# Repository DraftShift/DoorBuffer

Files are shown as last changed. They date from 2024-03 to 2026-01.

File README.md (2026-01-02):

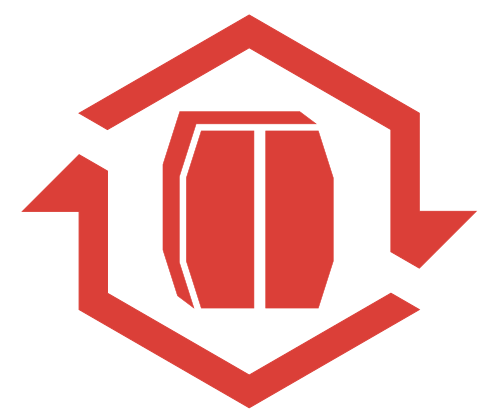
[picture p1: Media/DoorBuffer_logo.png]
#  DoorBuffer V2


&nbsp;&nbsp;&nbsp;&nbsp;&nbsp;&nbsp;


## 🌐 Official Website

StealthChanger now has an official website!

👉 **https://stealthchanger.com** 

##
Simple printable doorbuffer to claw back 15-20mm without upgrading the front frame. 

## WARNING: Calibrate shrinkage before you print. These are long pieces and errors will show.

### Now supports stock, Clacky, and Micron rev 1 doors

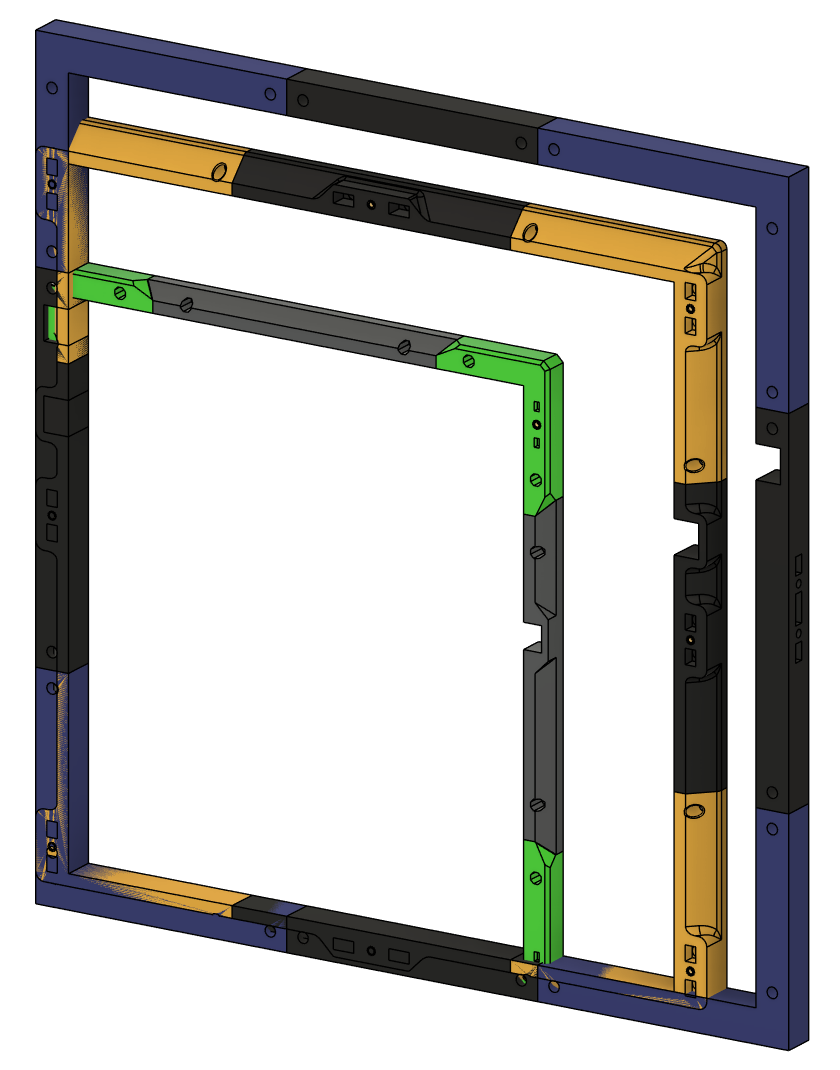
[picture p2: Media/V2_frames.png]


## BOM
Aditional hardware outside the doors
### Stock voron doors
* 22x M3 T-Nut
* 20x M3x8mm SHCS to hold the bracket
* 2x M3x20mm to hold the crossbar
* 8x M3 heat inserts for door mounting
### Klicky-Clack
* 22x M3 T-Nut
* 20x M3x8mm SHCS to hold the bracket
* 2x M3x20mm to hold the crossbar
* 6x M3 heat inserts for door 
### Micron
* 18x M3 nut
* 16x M3x8mm SHCS to hold the bracket
* 2x M3x16mm to hold the crossbar
* 4x M3 heat inserts for door 
* 2x M3x6mm FHCS for door magnets

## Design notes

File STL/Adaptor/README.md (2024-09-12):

# Doorbuffer Adapters

This mod allows you to use extrusions that are cut to the inside length of your front frame.

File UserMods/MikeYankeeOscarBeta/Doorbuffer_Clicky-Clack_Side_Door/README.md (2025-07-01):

# Doorbuffer Clicky-Clack Side Door

The Stock Voron V2 doors suck. Adding an additional 20mm more out the front to mount Clicky-Clack fridge door not too tempting?
Want to have access to your umbilicals and electronics on the back?
Feel like the docks are in the way when reaching for prints?

Add a ClickyClacky Fridge Door to the side of your printer instead with this mod!

## Description:
This Usermod replaces the right top and bottom corners of the door-buffer and uses most of the original parts from the Clicky-Clack Fridge door mod: https://github.com/tanaes/whopping_Voron_mods/blob/main/clickyclacky_door%2FREADME.md
Recommend using these hinges to move the side panel to the front so it's easily removeable: https://github.com/DraftShift/DoorBuffer/tree/main/UserMods/MikeYankeeOscarBeta/Doorbuffer_Side_Door_latches

It's designed for a 300 size Voron V2 with the normal height door-buffer, but should fit the other printer sizes for normal height docks.

by 
[MikeYankeeOscarBeta](https://github.com/MikeYankeeOscarBeta/) (VoronDesign Discord: #MikeyMike V2.5796, Voron Toolchangers Discord: MikeyMike - Github: [MikeYankeeOscarBeta](https://github.com/MikeYankeeOscarBeta/StealthChanger))
DraftShiftDesign Discord - user-project thread:    https://discord.com/channels/1226846451028725821/1243948065208008705

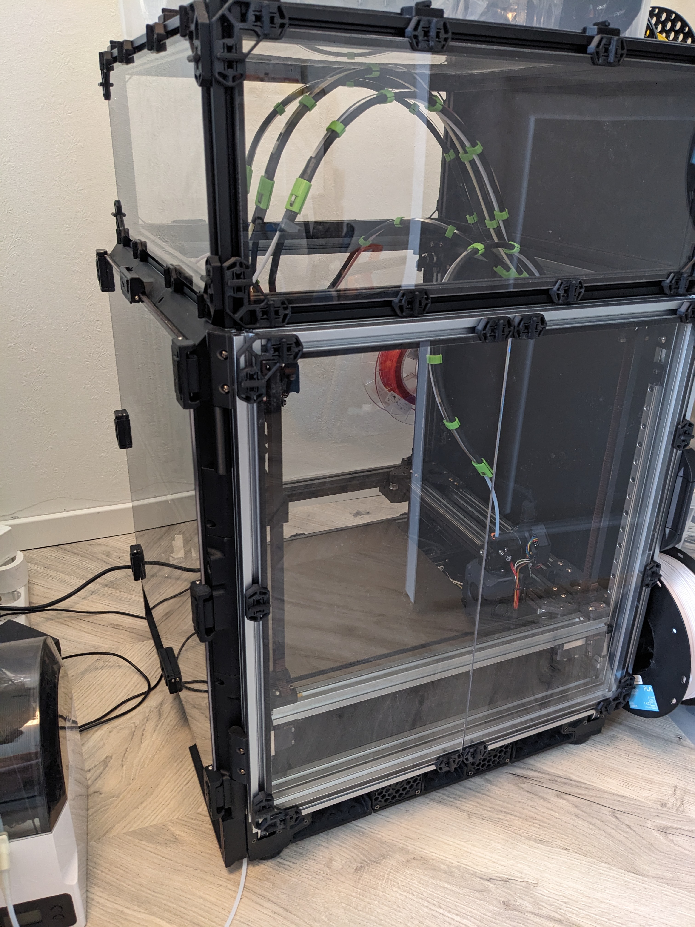
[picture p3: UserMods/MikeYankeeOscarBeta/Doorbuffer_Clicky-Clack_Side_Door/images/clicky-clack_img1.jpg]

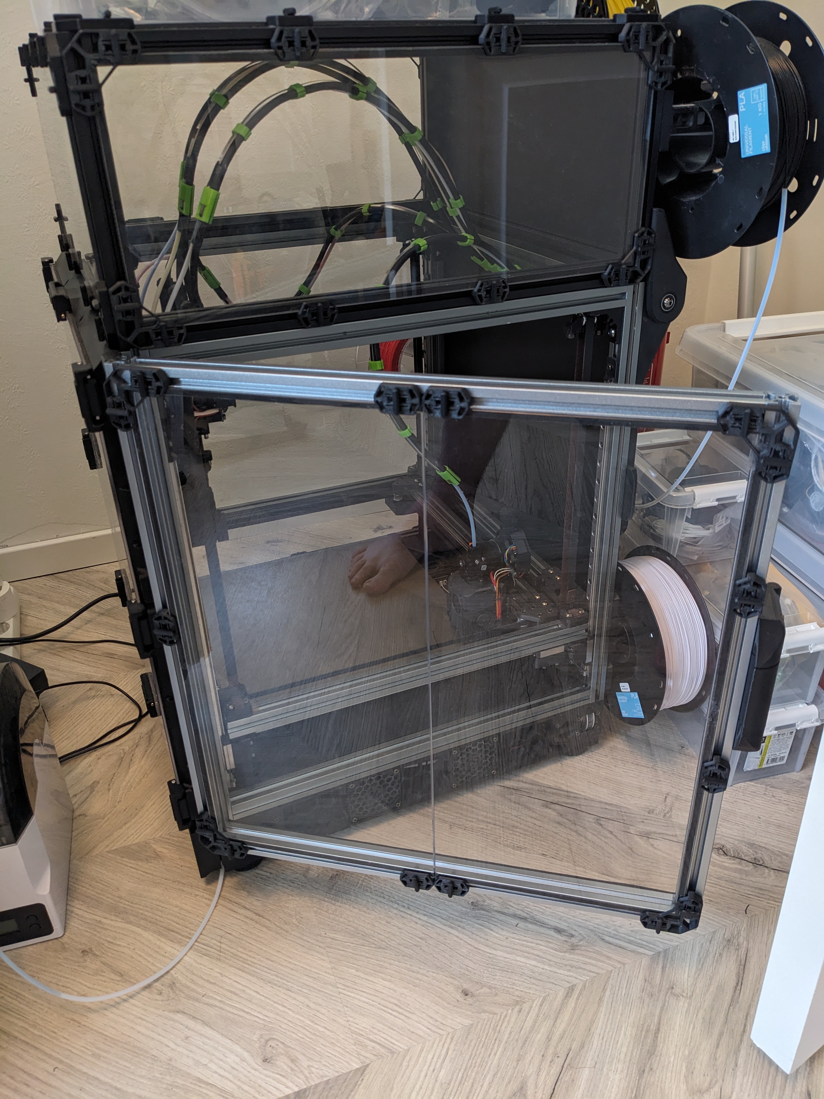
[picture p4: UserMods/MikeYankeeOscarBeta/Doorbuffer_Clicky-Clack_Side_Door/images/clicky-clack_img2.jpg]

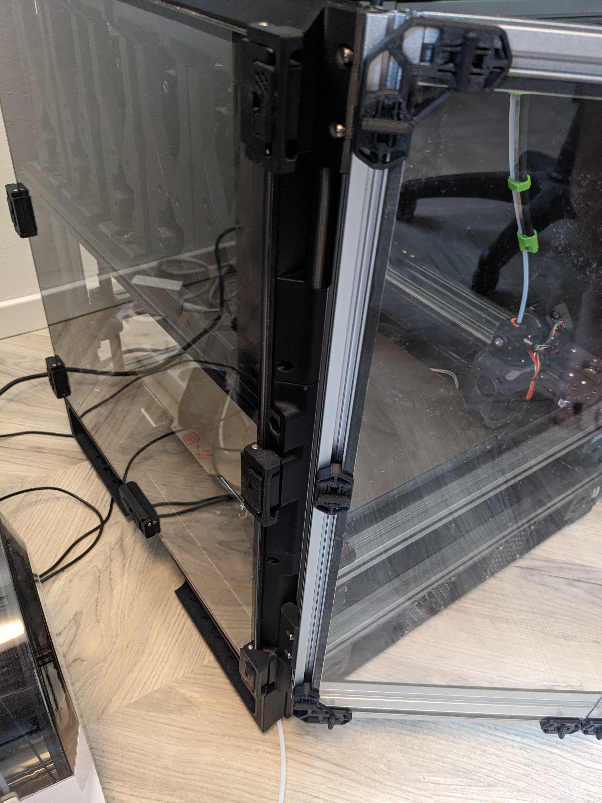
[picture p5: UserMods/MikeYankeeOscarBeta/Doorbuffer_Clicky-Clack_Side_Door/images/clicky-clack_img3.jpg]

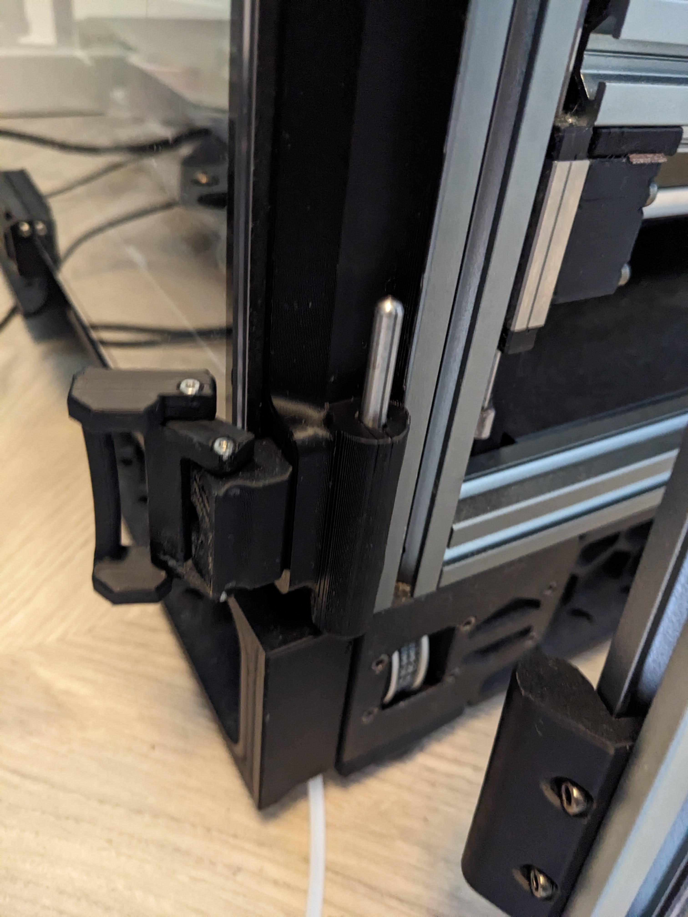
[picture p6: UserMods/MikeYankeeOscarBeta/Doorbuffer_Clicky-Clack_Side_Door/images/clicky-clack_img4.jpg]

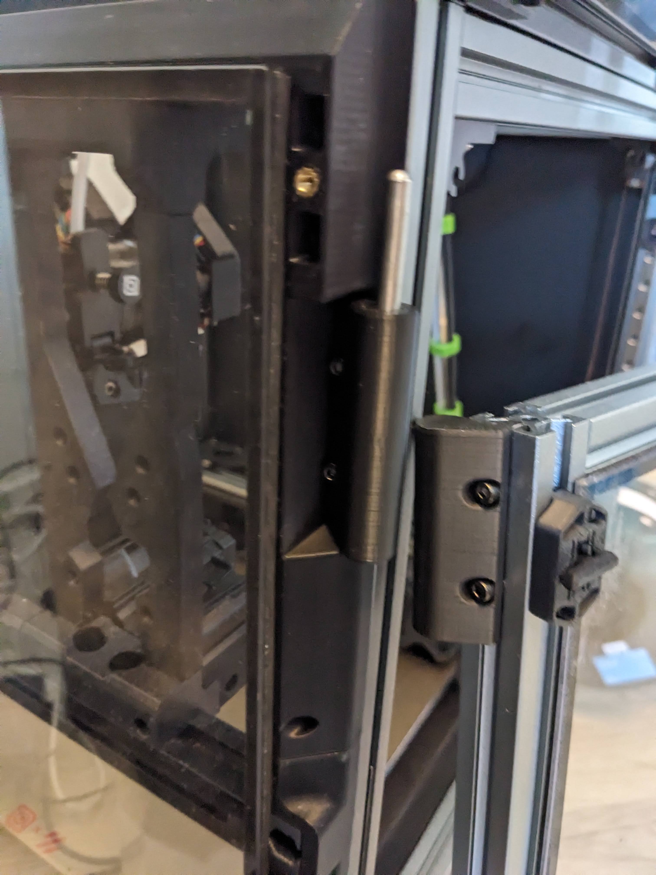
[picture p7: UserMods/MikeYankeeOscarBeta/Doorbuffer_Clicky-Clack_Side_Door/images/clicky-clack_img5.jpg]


## Parts to print:
- 1x doorbuffer-300-clickyclacky-sidedoor_A_v2.stl
- 1x doorbuffer-300-clickyclacky-sidedoor_A_v2.stl

## BOM:
Unchanged. It uses all the same hardware as door buffer and clicky-clack fridge door.

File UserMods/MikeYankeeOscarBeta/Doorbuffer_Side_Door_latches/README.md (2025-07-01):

# Doorbuffer Side Door Latches

Swap your door with your sidepanel with two door-buffers and some clips.

A simple blank and a remix of RichardM's amazing snap latches 
[Voron 2.4 Filament Latch (or any 2020 extrusion)](https://www.printables.com/model/172368-voron-24-filament-latch-or-any-2020-extrusion)  
- remixed for m2 screws and 5.5mm (3mmpanel + 3mm foam - 0.5mm compression)

by 
[MikeYankeeOscarBeta](https://github.com/MikeYankeeOscarBeta/) (VoronDesign Discord: #MikeyMike V2.5796, Voron Toolchangers Discord: MikeyMike - Github: [MikeYankeeOscarBeta](https://github.com/MikeYankeeOscarBeta/StealthChanger))
DraftShiftDesign Discord - user-project thread:    https://discord.com/channels/1226846451028725821/1243948065208008705

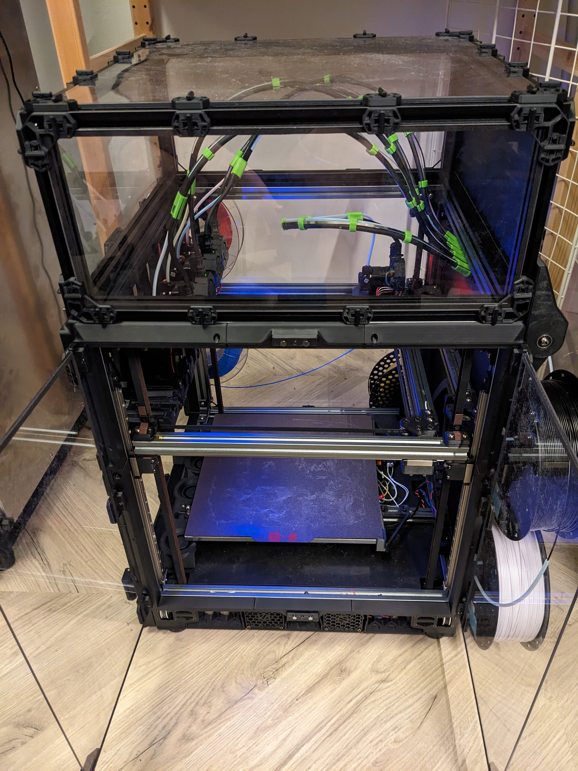
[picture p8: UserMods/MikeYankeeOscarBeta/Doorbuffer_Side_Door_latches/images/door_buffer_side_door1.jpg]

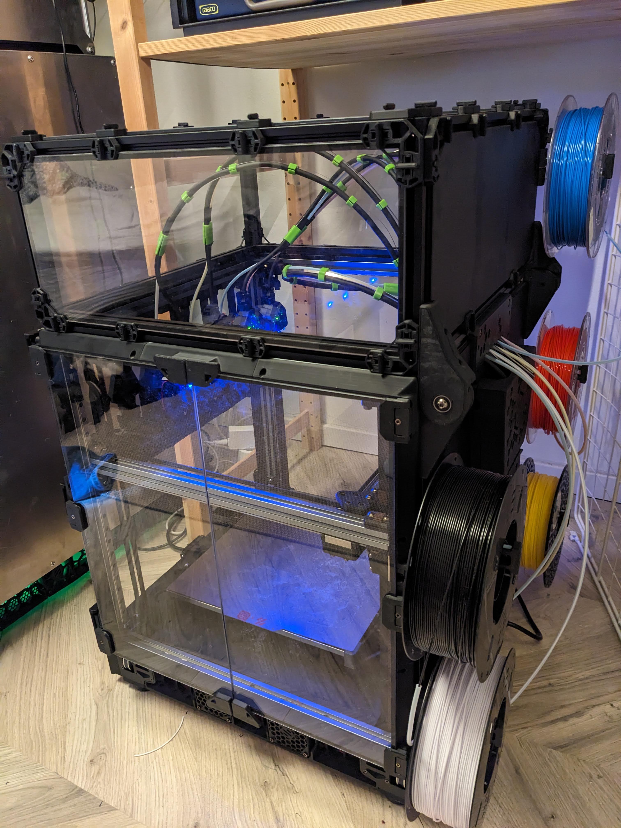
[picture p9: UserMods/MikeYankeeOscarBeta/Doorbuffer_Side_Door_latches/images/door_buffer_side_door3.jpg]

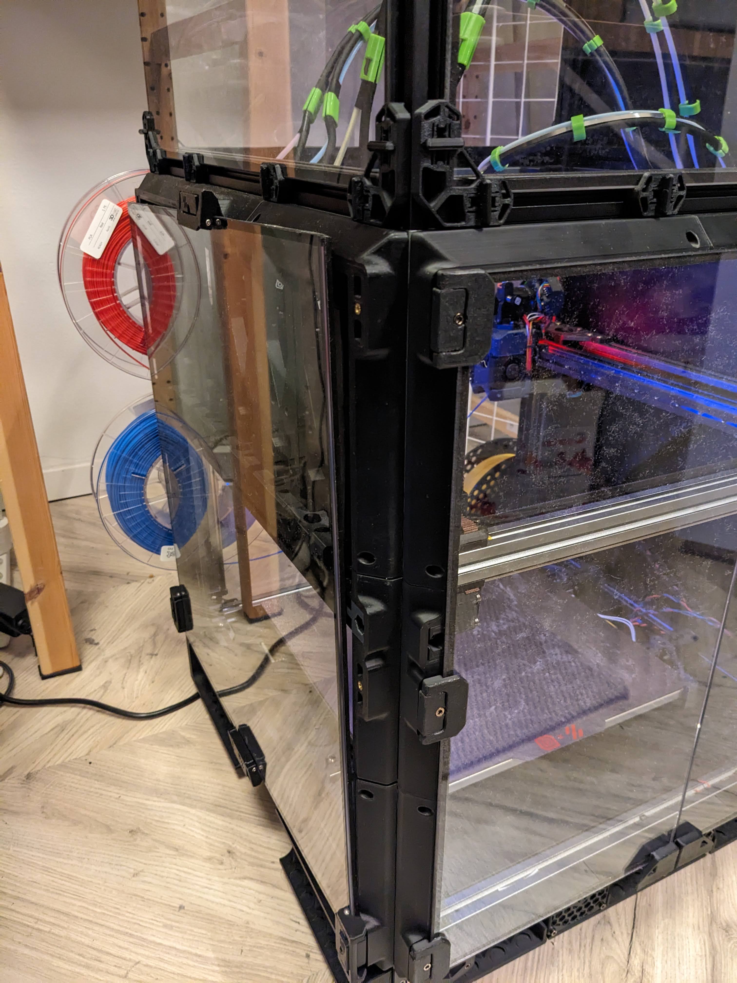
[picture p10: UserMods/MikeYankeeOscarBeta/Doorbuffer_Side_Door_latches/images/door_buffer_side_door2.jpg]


## Parts to print:
- 2x Door Buffer
- 2x NewLatchWithHandle_m2x10mmSHCS_screw_normal_size_3mm_panel_3mm_foam_2_long.stl
- 6x NewLatchWithHandle_m2x10mmSHCS_screw_normal_size_3mm_panel_3mm_foam_2.stl
- 2x 2020_doorbuffer_adapter_blank_for_M5x16_BHCS_x2.stl

## BOM per latch (need 6 latches in total):
| Part | for | Amount | Description|
|---|---|---|-|
| M3x12-14mm BHCS/SHCS Screw  | latch | 6 | M3 BHCS/SHCS screw |
| M2x15mm SHCS Screw | latch | 4 | M2 SHCS screw |
| M3x25mm SHCS Screw | latch | 4 | M2 SHCS screw |
| M5x16 BHCS Screw | Adapter | 2 | M5 BHCS/SHCS |

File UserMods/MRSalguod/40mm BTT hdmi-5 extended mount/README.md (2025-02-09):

An extended bbt hdmi-5 mount for use with the [Clicky-Clack Fridge Door](https://github.com/tanaes/whopping_Voron_mods/tree/main/clickyclacky_door) 
and the [DraftShift Design](https://github.com/DraftShift) [Door Buffer v2](https://github.com/DraftShift/DoorBuffer).   [(Printables Link)](https://www.printables.com/model/1066444)

Print with regular voron recommended settings.

You will need to print 1 of each of the parts from the STL folder. No supports needed.   

Remixed from @DETMan's BTT HDMI5 Mount for Clicky Clack Door for use with the DraftShift Design Door Buffer.   [(Printables Link)](https://www.printables.com/model/861544)

Whom remixed it from @EDnation.   [(Printables Link)](https://www.printables.com/model/787236)

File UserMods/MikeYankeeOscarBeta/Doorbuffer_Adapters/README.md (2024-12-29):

# Doorbuffer Adapters for Monolith_Crossbar
based on DoorBuffer Adapter by [TheSin-](https://github.com/TheSin-/) 

Monolith AWD mod by [MikeYankeeOscarBeta](https://github.com/MikeYankeeOscarBeta/) (VoronDesign Discord: #MikeyMike V2.5796, Voron Toolchangers Discord: MikeyMike - Github: [MikeYankeeOscarBeta](https://github.com/MikeYankeeOscarBeta/StealthChanger))
DraftShiftDesign Discord - user-project thread:    https://discord.com/channels/1226846451028725821/1243948065208008705

This mod allows you to use extrusions that are cut to the inside length of your front frame for monolith adapters.

### Only tested with R0 Printed Monolith AWD (pre-live shaft version)

Printable adapters for crossbar to clear monolith AWD front motors for Voron V2 with StealthChanger

Have to cut the 2020 to size.
The monolith AWD motors take 45mm on each side so the 2020 has to be 90mm shorter than the frames horizontal extrusions

## BOM:
| Part | Amount | Description |
|---|---|---|
| M3 T-slot nut | 4 | Any M3 2020 T-Slot Nut will work (recommend springnuts) |
| M5x15mm BHCS/SHCS Screw | 2 | M5 BHCS/SHCS socket head screw, 15mm minimum (longer is better if you can tap the extrusion deeper than 10mm) |
| M3x20mm SHCS Screw | 4 | M3 screw, BHCS will also work |
| 2020 extrusion | 1 | 2020 extrusion cut to length (see table below), tapped on both ends. Misumi#: HFS5-2020-380-TPW  / HFSB5-2020-380-TPW |
| M3x25mm SHCS Screw | 4 | M3 screw, BHCS will also work |

### Extrusion lengths for Stock V2 sizes:
| Model | Calculation | Monolith AWD Crossbar extrusion length |
|---|---|---|
| Voron V2-350 | 470.00 mm - 90mm | 380 mm |
| Voron V2-300 | 420 mm - 90mm | 330 mm |
| Voron V2-250 | 370 mm - 90mm | 280 mm |
| Voron V2-custom size  | [horizontal extrusion length] - 90mm | x mm |

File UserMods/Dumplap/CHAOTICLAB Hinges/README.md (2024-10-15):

Door Buffer modified to fit the 2 hinge CNC door hinges from CHAOTICLAB

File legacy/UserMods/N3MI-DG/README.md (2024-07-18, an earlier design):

# Short Frame Buffer Mod

This mod add door buffer support for <a href="https://github.com/DraftShift/ModularDock/tree/main/UserMods/BlackShade/ShortFrame">BlackShade's Short Frame Dock Mod</a> for both 300mm and 350mm frames. It replaces the left and right middle sections of the door buffer and both T slot (default) and V slot versions are provided.

### Extra BOM
2x M3 6mm SHCS screws

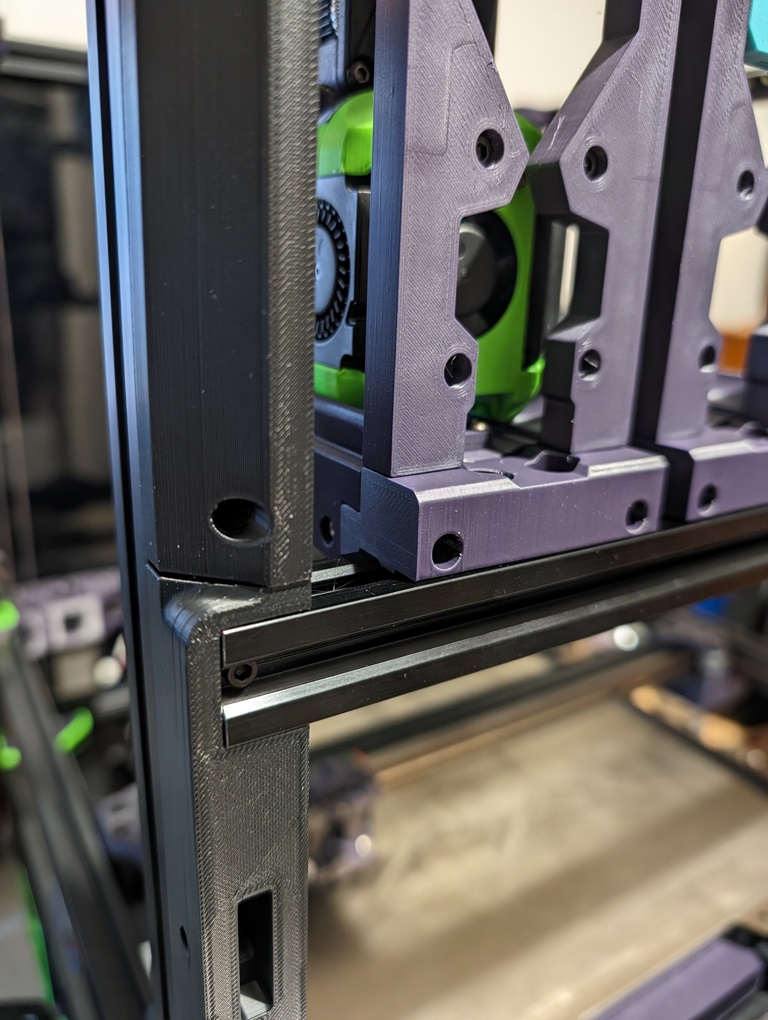
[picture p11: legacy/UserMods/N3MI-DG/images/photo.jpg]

<br/>
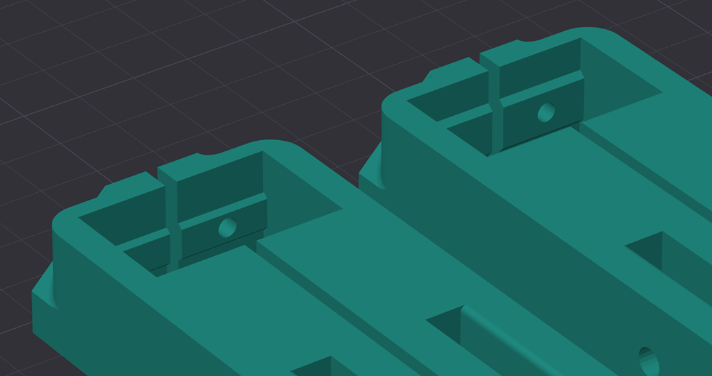
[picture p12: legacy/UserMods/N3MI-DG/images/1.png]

<br/>
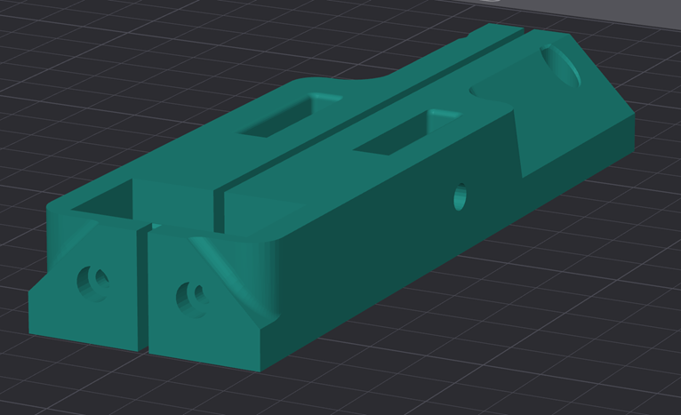
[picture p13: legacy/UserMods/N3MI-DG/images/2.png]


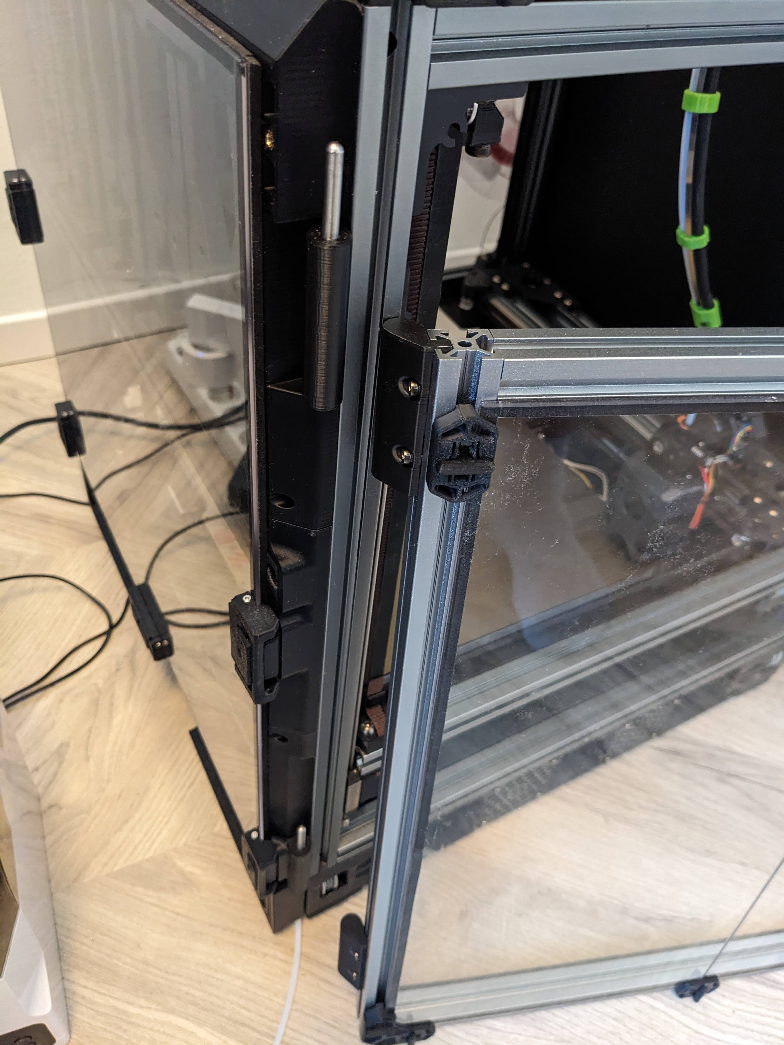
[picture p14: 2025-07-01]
UserMods/MikeYankeeOscarBeta/Doorbuffer_Clicky-Clack_Side_Door/images/clicky-clack_img6.jpg

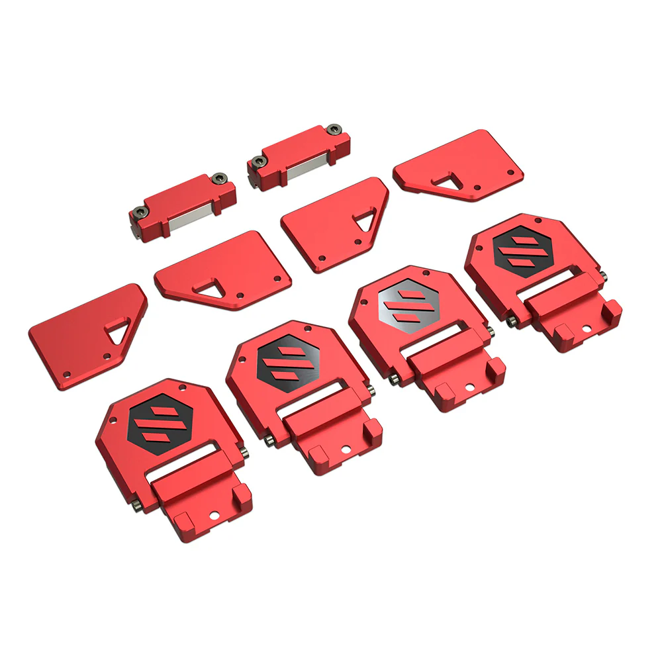
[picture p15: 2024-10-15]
UserMods/Dumplap/CHAOTICLAB Hinges/Media/CNChing.png

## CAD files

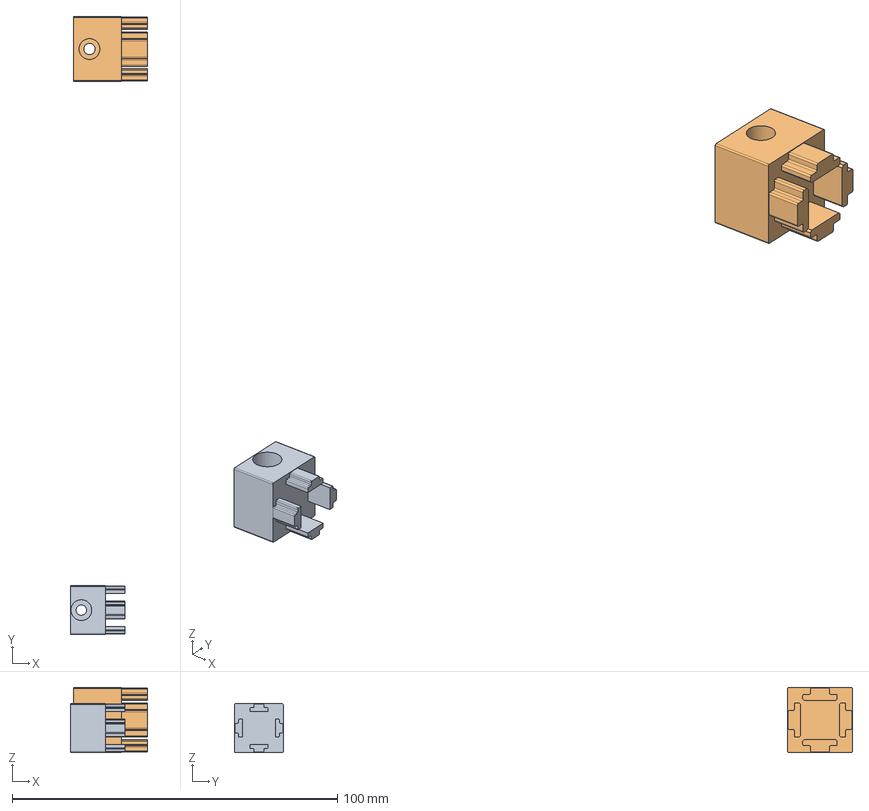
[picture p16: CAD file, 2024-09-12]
CAD/Doorbuffer_Adapters.step
23.8 x 190.0 x 20.0 mm
1515_doorbuffer_adapter_x2
2020_doorbuffer_adapter_x2

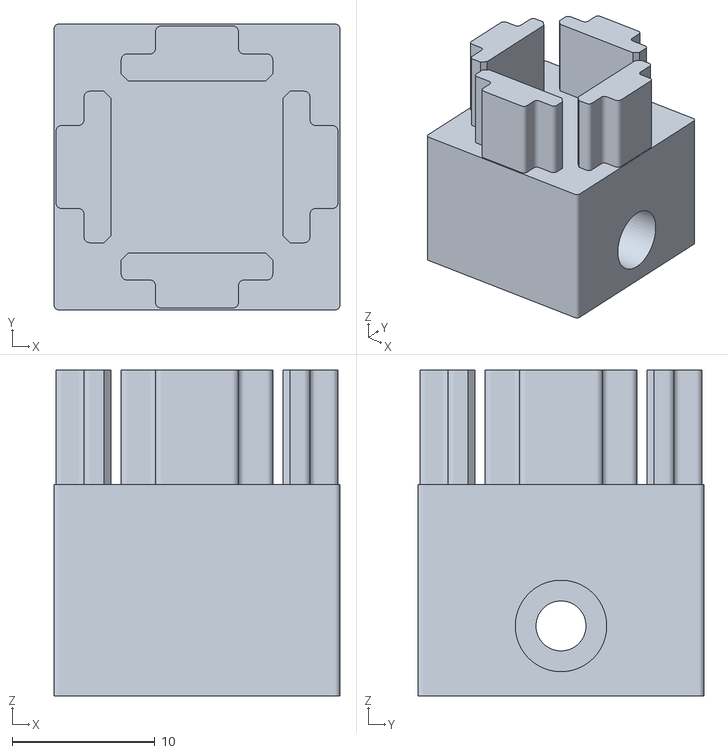
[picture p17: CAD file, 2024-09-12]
STL/Adaptor/2020_doorbuffer_adapter_x2.stl
20.0 x 20.0 x 22.8

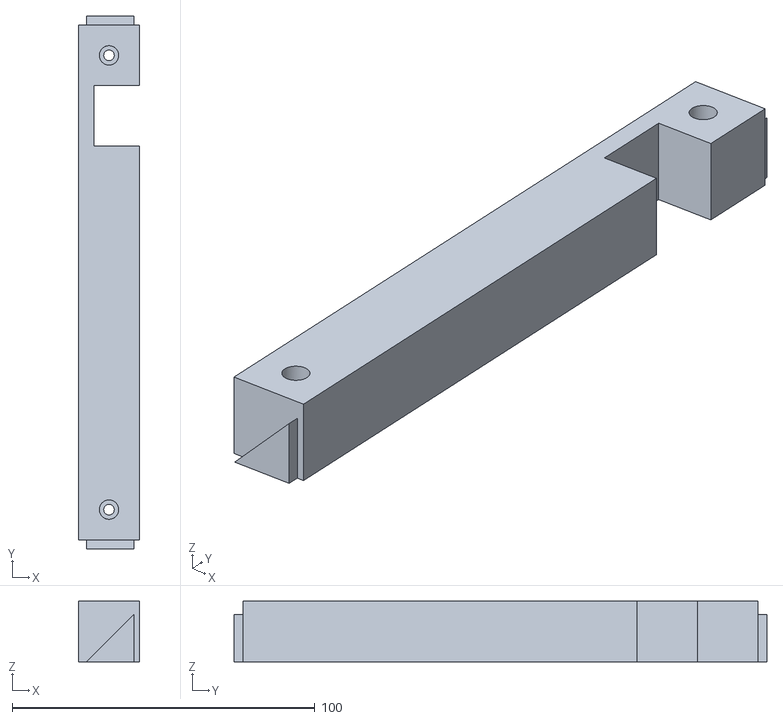
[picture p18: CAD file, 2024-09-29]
STL/Clicky-Klack/Short docks/250/Left.stl
20.0 x 176.0 x 20.0

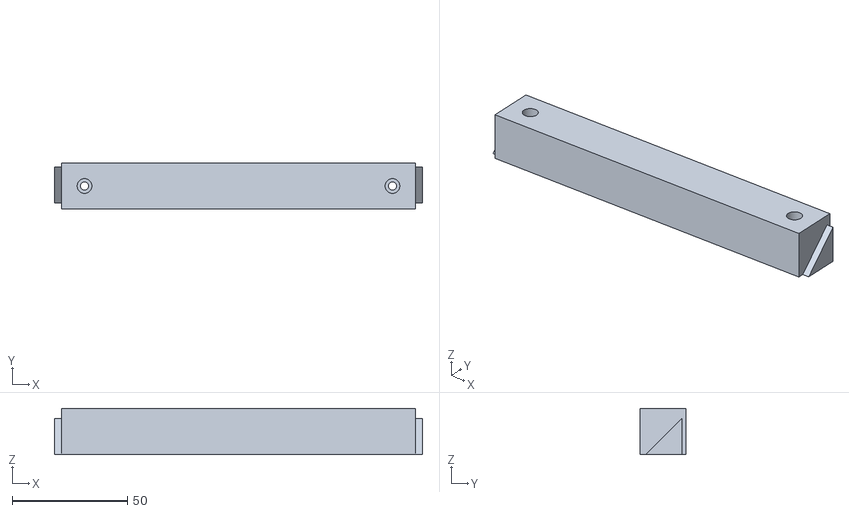
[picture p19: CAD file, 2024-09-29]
STL/Clicky-Klack/Short docks/300/Bottom.stl
159.3 x 20.0 x 20.0

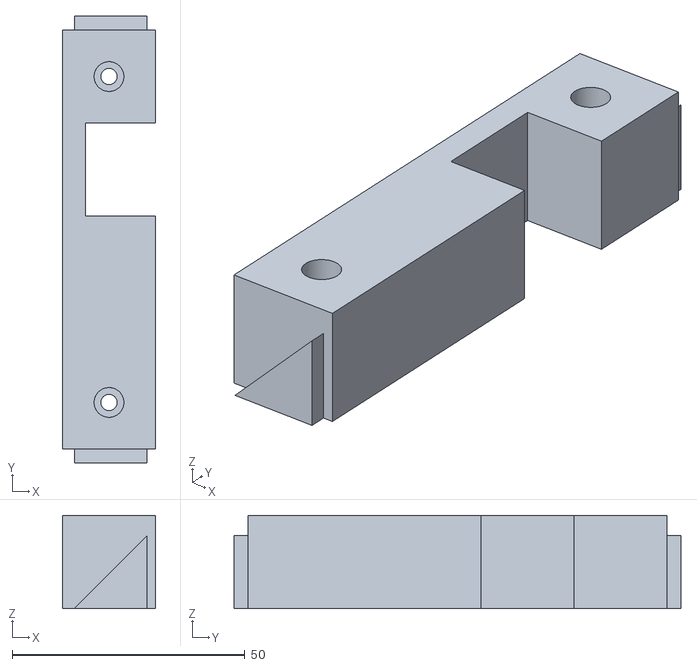
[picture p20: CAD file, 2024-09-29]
STL/Clicky-Klack/Standard docks/250/Left.stl
20.0 x 96.0 x 20.0

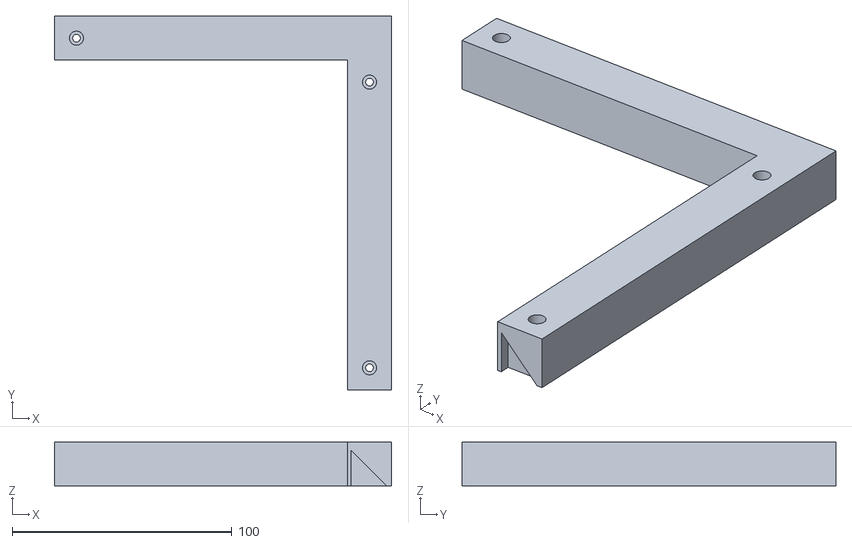
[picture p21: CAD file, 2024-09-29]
STL/Clicky-Klack/Standard docks/300/Top right corner.stl
153.3 x 170.0 x 20.0

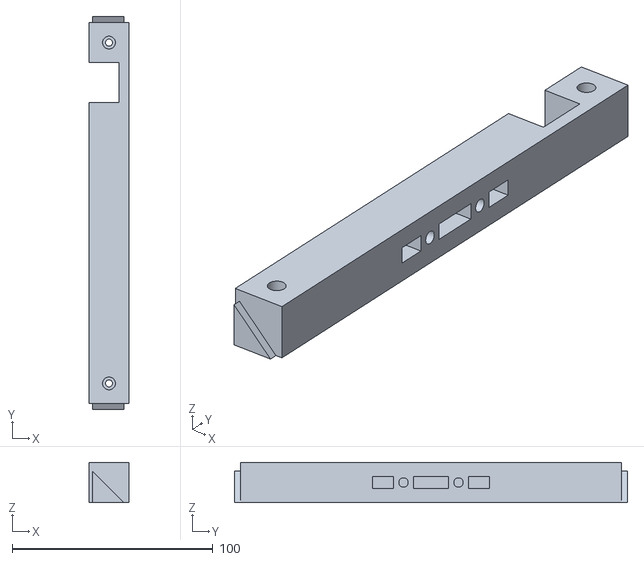
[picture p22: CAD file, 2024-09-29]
STL/Clicky-Klack/Standard docks/350/Right.stl
20.0 x 196.0 x 20.0

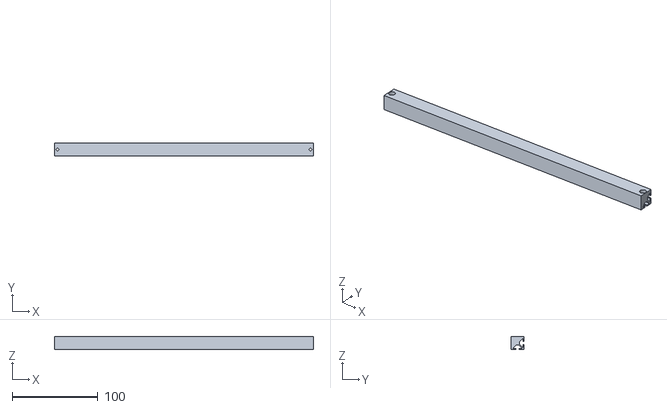
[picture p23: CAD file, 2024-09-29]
STL/Micron/Micron dockbar.stl
302.0 x 15.0 x 15.0

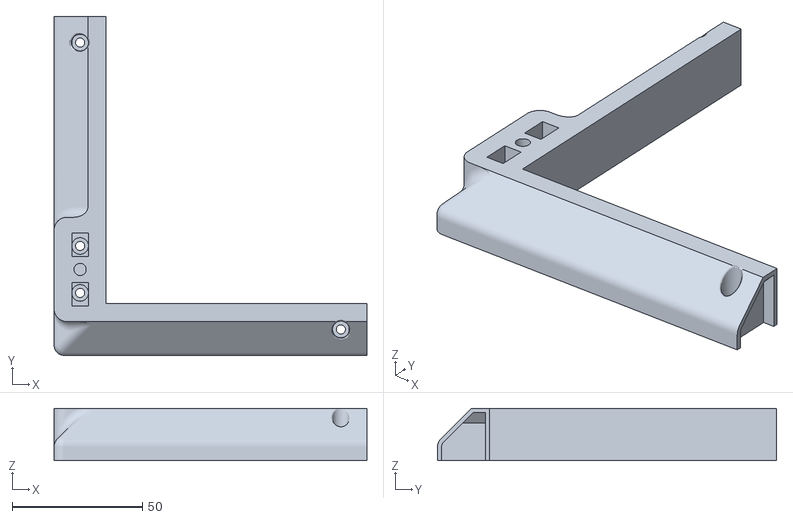
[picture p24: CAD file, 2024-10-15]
STL/Stock Voron/Short docks/300/Bottom left corner.stl
120.0 x 130.0 x 20.0

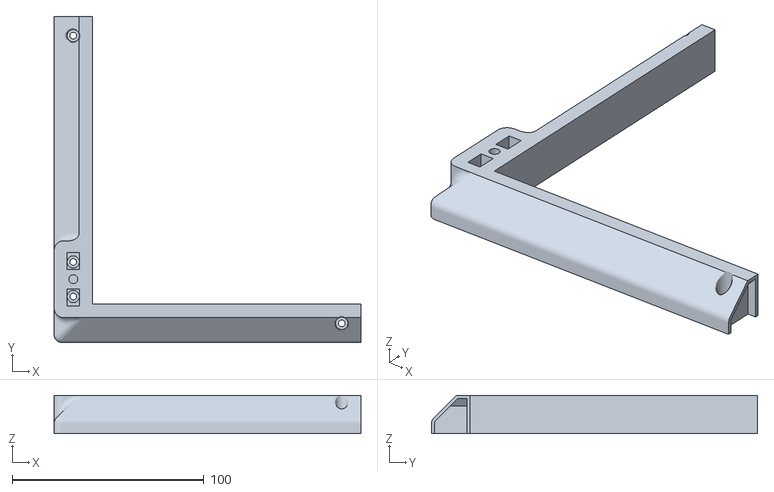
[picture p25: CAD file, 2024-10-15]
STL/Stock Voron/Standard docks/300/Bottom left corner.stl
160.0 x 170.0 x 20.0

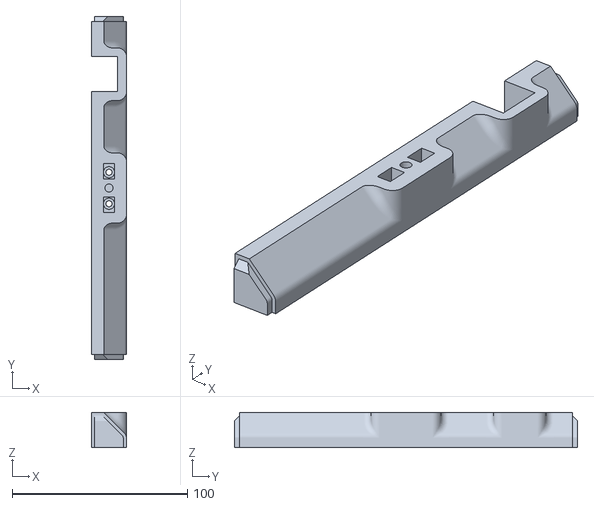
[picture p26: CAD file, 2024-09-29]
STL/Stock Voron/Standard docks/350/Left.stl
20.0 x 196.0 x 20.0

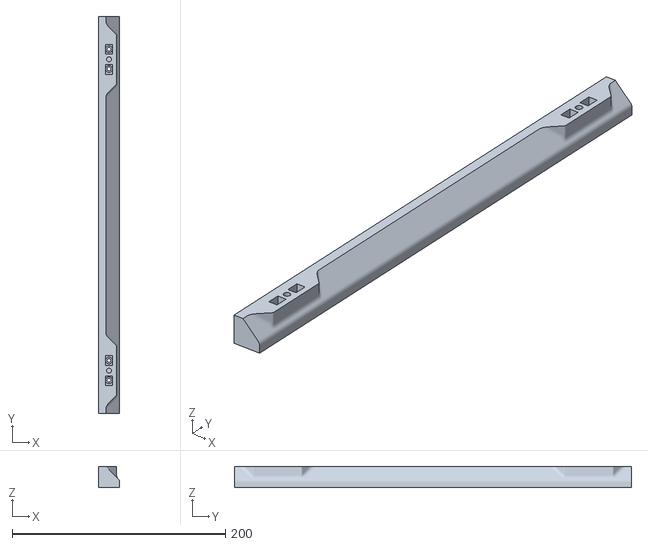
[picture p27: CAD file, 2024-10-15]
UserMods/Dumplap/CHAOTICLAB Hinges/STL/Right.stl
20.0 x 372.2 x 20.0

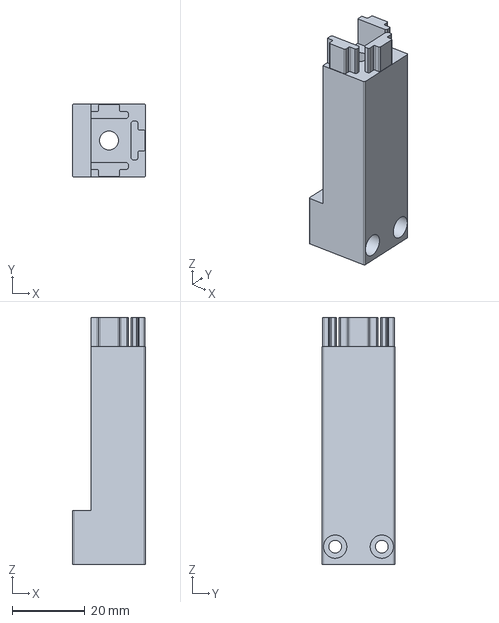
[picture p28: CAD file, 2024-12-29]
UserMods/MikeYankeeOscarBeta/Doorbuffer_Adapters/CAD/2020_doorbuffer_adapter_monolith.step
20.0 x 20.0 x 67.8 mm

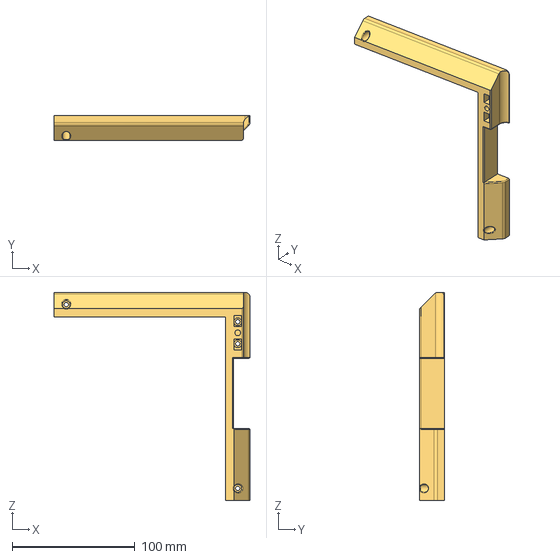
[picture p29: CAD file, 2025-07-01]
UserMods/MikeYankeeOscarBeta/Doorbuffer_Clicky-Clack_Side_Door/CAD/doorbuffer-300-clickyclacky-sidedoor_B_v2.step
160.0 x 20.0 x 170.0 mm

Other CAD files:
STL/Clicky-Klack/Short docks/350/Top.stl
STL/Stock Voron/Short docks/250/Top.stl
STL/Stock Voron/Short docks/350/Bottom right corner.stl
STL/Stock Voron/Standard docks/250/Bottom.stl
STL/Adaptor/1515_doorbuffer_adapter_x2.stl
STL/Clicky-Klack/Short docks/250/Bottom left corner.stl
STL/Clicky-Klack/Short docks/250/Bottom right corner.stl
STL/Clicky-Klack/Short docks/250/Bottom.stl
STL/Clicky-Klack/Short docks/250/Right.stl
STL/Clicky-Klack/Short docks/250/Top left corner.stl
STL/Clicky-Klack/Short docks/250/Top right corner.stl
STL/Clicky-Klack/Short docks/250/Top.stl
STL/Clicky-Klack/Short docks/300/Bottom left corner.stl
STL/Clicky-Klack/Short docks/300/Bottom right corner.stl
STL/Clicky-Klack/Short docks/300/Left.stl
STL/Clicky-Klack/Short docks/300/Right.stl
STL/Clicky-Klack/Short docks/300/Top left corner.stl
STL/Clicky-Klack/Short docks/300/Top right corner.stl
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

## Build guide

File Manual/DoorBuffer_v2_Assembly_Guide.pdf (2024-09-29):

# Door Buffer V2

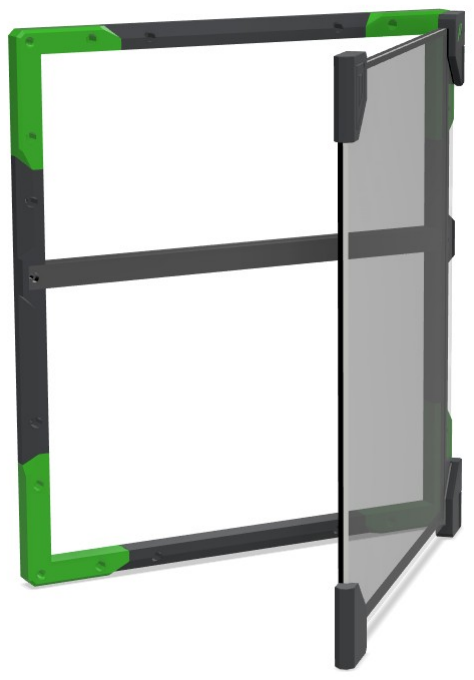
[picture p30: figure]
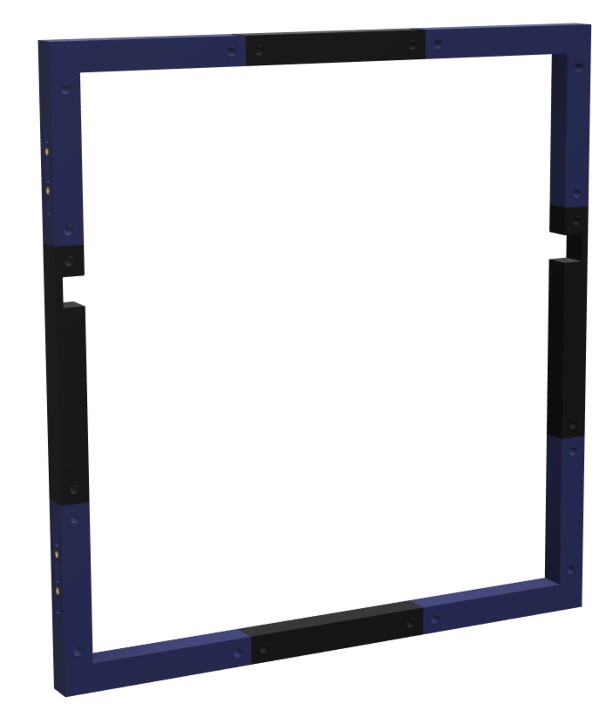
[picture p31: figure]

# Door Buffer V2 BUILD GUIDE

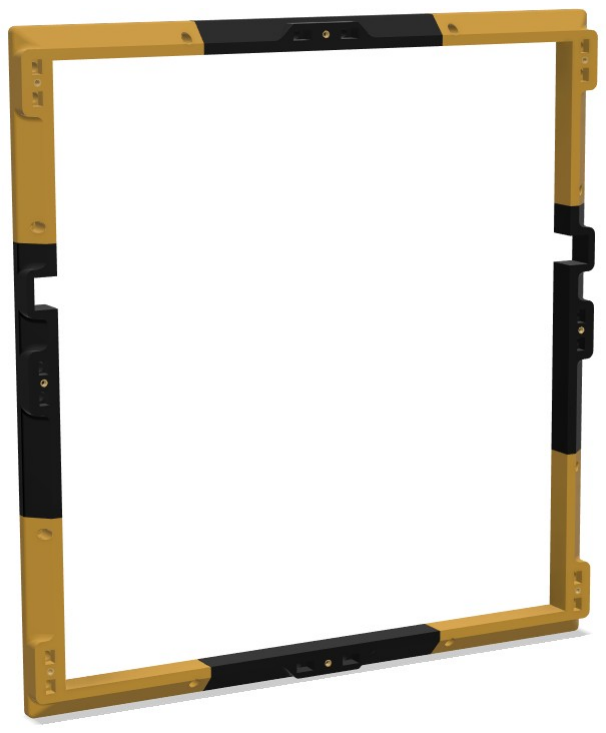
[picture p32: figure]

# Giving you 20mm back, and a more rigid dock (Now with Micron and Clacky support)

# VERSION 2024-09-28

## PREFACE

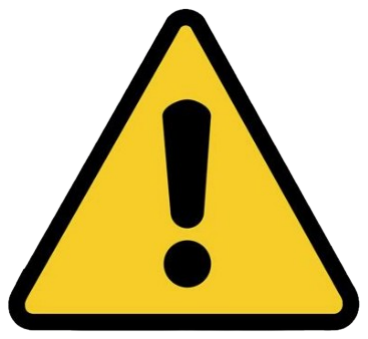
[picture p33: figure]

Before you begin on your journey, a word of caution.

In the comfort of your own home you are about to assemble a robot. This machine can maim, burn, and electrocute you if you are not careful. Please do not become the first STEALTHCHANGER fatality. There is no special Reddit flair for that.

Please, read the entire manual before you start assembly. As you begin wrenching, please check our Discord channels for any tips and questions that may halt your progress.

Most of all, good luck!

THE STEALTHCHANGER TEAM

2

## GITHUB.COM/STEALTHCHANGER/DOORBUFFER

## TABLE OF CONTENTS

Introduction | 04
Hardware | 07
New features | 08
Frame | 9
Heat inserts | 11
Attach to frame | 12
Mounting doors | 13
Parametric editing | 15

3

## INTRODUCTION

PART PRINTING GUIDELINES

The Voron Team has provided the following print guidelines for you to follow in order to have the best chance at success with your parts. The StealthChanger Team recommends to follow the same standards. There are often questions about substituting materials or changing printing standards, but we recommend you follow these:

3D PRINTING PROCESS
Fused Deposition Modeling (FDM)

MATERIAL
ABS

LAYER HEIGHT
Recommended: 0.2mm

EXTRUSION WIDTH
Recommended: Forced 0.4mm

INFILL TYPE
Grid, Gyroid, Honeycomb, Triangle or Cubic

INFILL PERCENTAGE
Recommended: 15% or higher

NOTE: These parts do not experience any load an can be less dense compared to other Voron parts

WALL COUNT
Recommended: 4

SOLID TOP/BOTTOM LAYERS
Recommended: 5

4

## INTRODUCTION

FILE NAMING

By this time you should have already downloaded our STL files from the StealthChanger GitHub. You might have noticed that we have used the Voron naming convention for the files. This is how to use them.

PRIMARY COLOUR

Example part_x4.stl

These files will have nothing at the start of the filename.

ACCENT COLOUR

Example [a]_part.stl

We have added “[a]” to the front of any STL file that is intended to be printed with accent colour.

QUANTITY REQUIRED

Example [a]_part_x4.stl

If any file ends with “_x#”, that is telling you the quantity of that part required to build the machine.

HOW TO GET HELP

If you need assistance with your build, we are here to help. Head on over to our Discord group and post your questions. This is our primary medium to help STEALTHCHANGER Users and we have a great community that can help you out if you get stuck.

### https://discord.gg/Mx9JKbt7

5

## INTRODUCTION

REPORTING ISSUES

Should you find an issue in the documentation or have a suggestion for an improvement please consider opening an issue on GitHub (https://github.com/Stealthchanger/DoorBuffer/issues). When raising an issue please include the relevant page numbers and a short description; annotated screenshots are also very welcome. We periodically update the manual based on the feedback we get.

THIS IS JUST A REFERENCE

This manual is designed to be a simple reference manual and we always recommend downloading the cad-files to look around for yourself.

### https://github.com/Stealthchanger/DoorBuffer

6

## HARDWARE REFERENCE

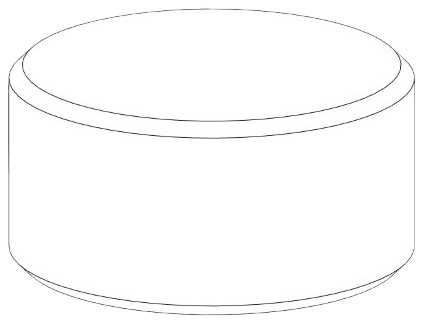
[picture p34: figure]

MAGNET Metric round button neodymium magnet used on the Voron. N52 is highly recommended. | SOCKET HEAD CAP SCREW (SHCS) Metric fastener with a cylindrical head and hex drive. The most common fastener used on the Voron. ISO 4762

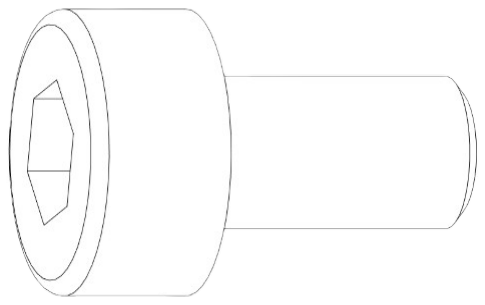
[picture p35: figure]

T-NUT Hammerhead A type of nut that slides into the extrusion rail as a method of affix other parts to it. | HEAT SET INSERT Heat inserts with a soldering tip so that they melt the plastic when installed. As the plastic cools, it solidifies around the knurls and ridges on the insert for excellent resistance to both torque and pull-out.

7

## NEW FEATURES

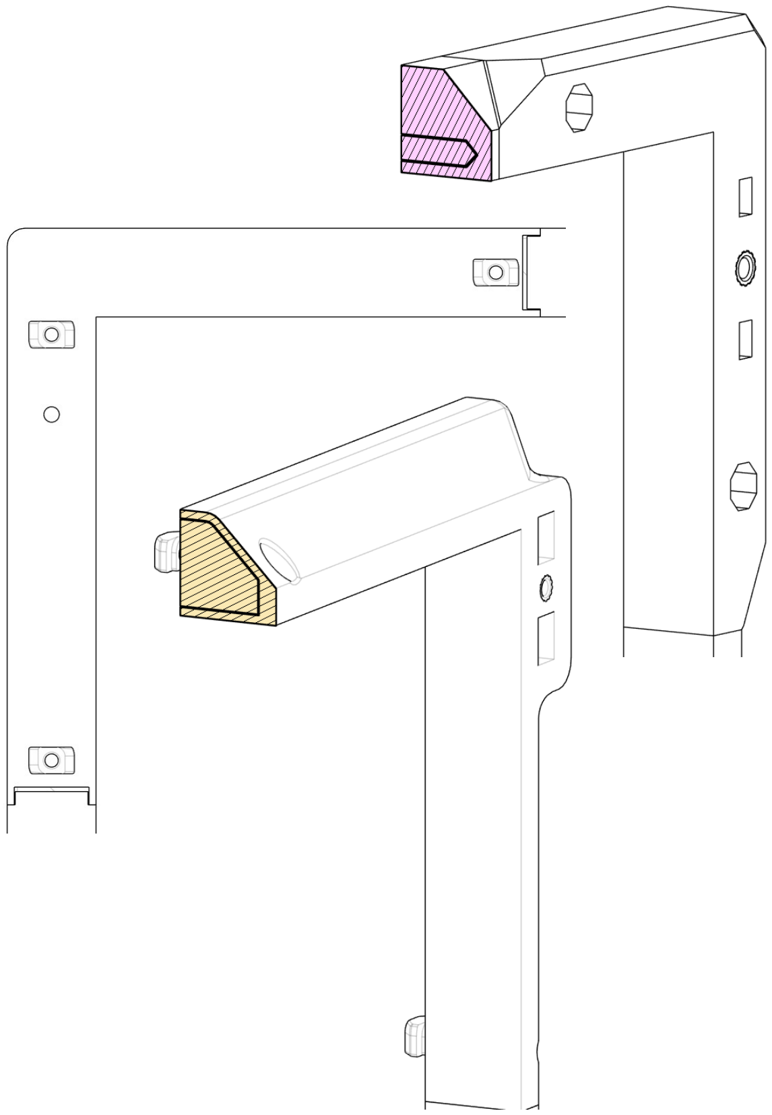
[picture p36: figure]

Stock panels

- Gone are the decorative clips in favour of a simpler design
- Adjustable dockheights (130mm to 170mm) to accommodate stubby docks.

Klacky door

The build now adds klackydoors! This is only a simple plastic 2020 padding, but can be configured with the parametric file if needed.

Micron door!

The micron buffer is designed specifically for short docks.

NOTE: The door is taken from the rev 1 version found on their Github (https://github.com/PrintersForAnts/Micron/tree/main)

Common new features

All variations come with overlapping design to help patch those pesky gaps!

8

## FRAME

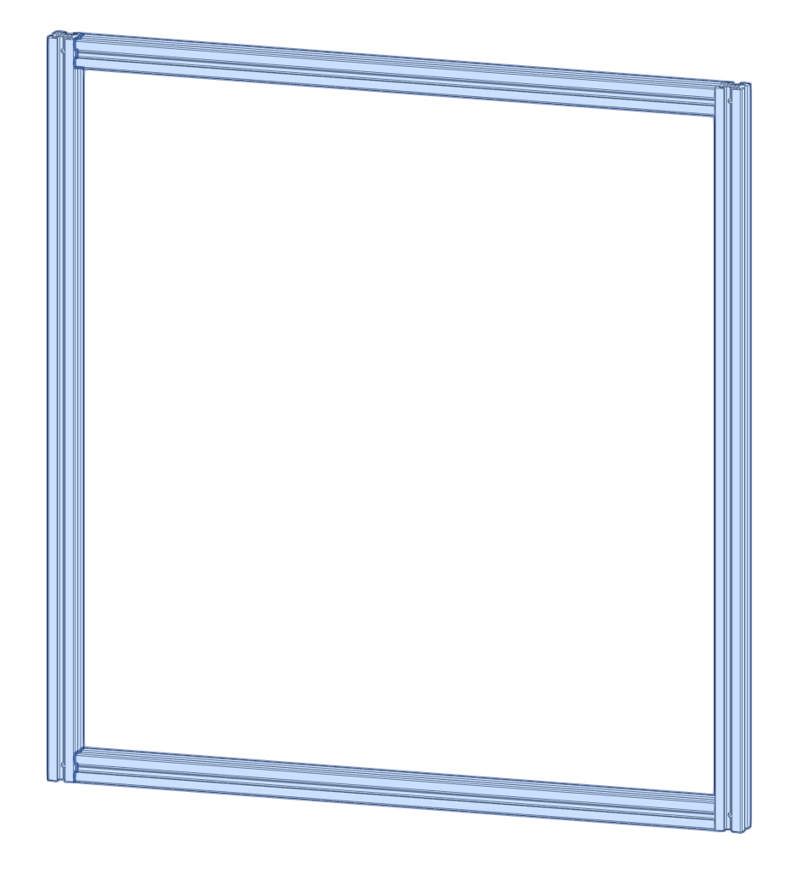
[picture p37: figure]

BASE FRAME

This build is meant to attach onto a normal 2020 V2.4 frame, though if you have a customized one there will be instructions on how to edit this entire design in Fusion360 at the end.

NOTE: before you begin printing, measure to see if your frame is actually up to Voron specs. A few mm off will create gaps in your parts. If its out of spec. Look at the end of this manual and enter your real measurements into the parametric CAD file!

NOTE: Make sure your printer is properly calibrated for dimensions and material shrinkage! As some of these parts can get long a small deviation will give noticeable results!

TOOLBAR HOLE PLACEMENT
The bottom bar that the modular docks mount to is 10mm shorter than your frame measured furthest left to right. A standard 350 frame is 510mm across the front and so the toolbar needs to be 500mm

NOTE: You will need to drill a hole big enough for a 3mm screw to pass through 4mm minimum is recommended for better adjustment.

NOTE:
Micron bar is 302mm. 8Mm shorter than the total width of the micron.

9

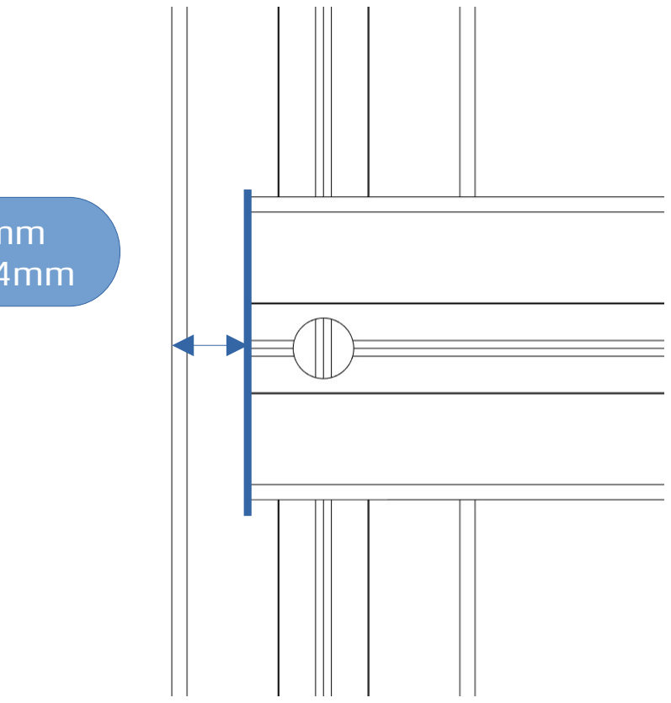
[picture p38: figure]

2.4 = 5mm

## Micron = 4mm

## FRAME

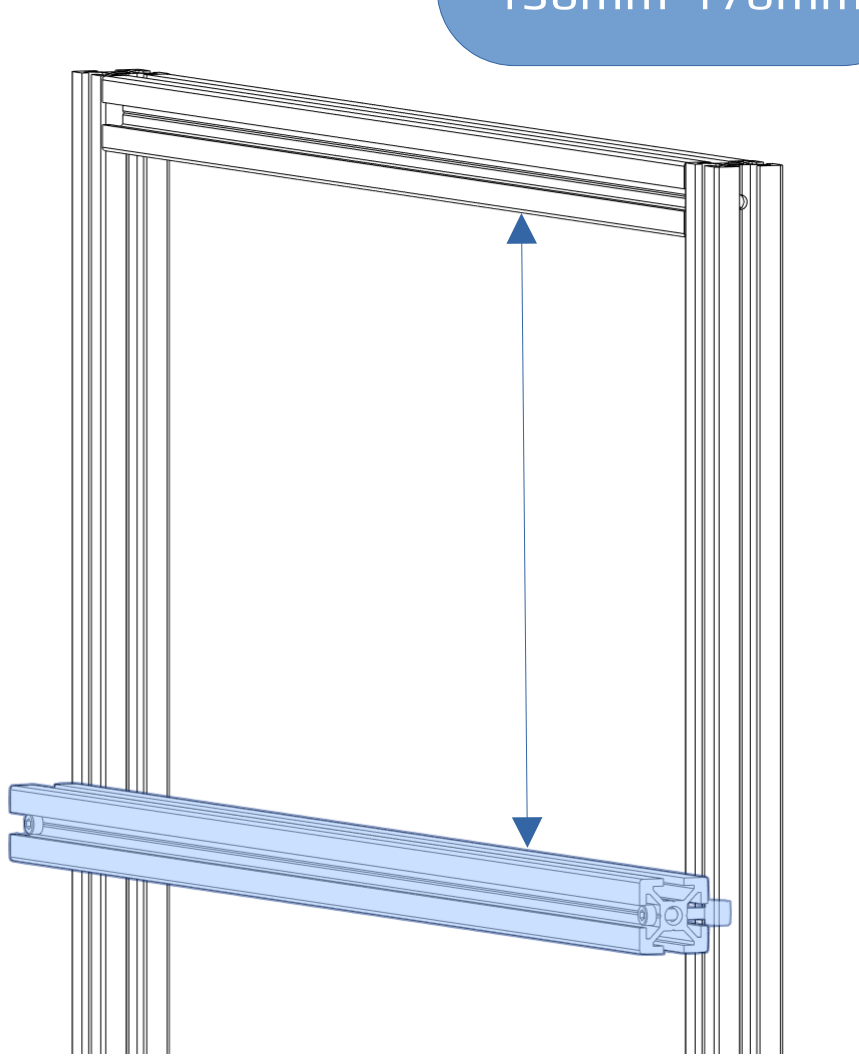
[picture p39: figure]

TOOLBAR TO FRAME

The new V2 buffer supports any dock height from 130mm to 170mm so make sure you bolt on the extrusion at correct height.

NOTE:
- For a standard dock height, use 170mm
- For stubby docks, use 130mm

EXTRA NOTE:
Micron only supports 130mm docks!

## 130mm-170mm

SCREWS

Take your M3x20mm through the holes you made and mount it using T-NUT’s

## M3x20mm SHCS T-NUT

10

ATTENTION MICRON BUILDERS!

For preloading nuts you have to add 4xM3 nuts to BOTH top and bottom horizontal extrusions, the vertical ones have free access and can be added later without worry.

Also for attaching the extrusion M3x12mm or 16mm may be needed depending on your extrusion profile. Check clearances and potentially add a washer for correct spacing

## Heat inserts

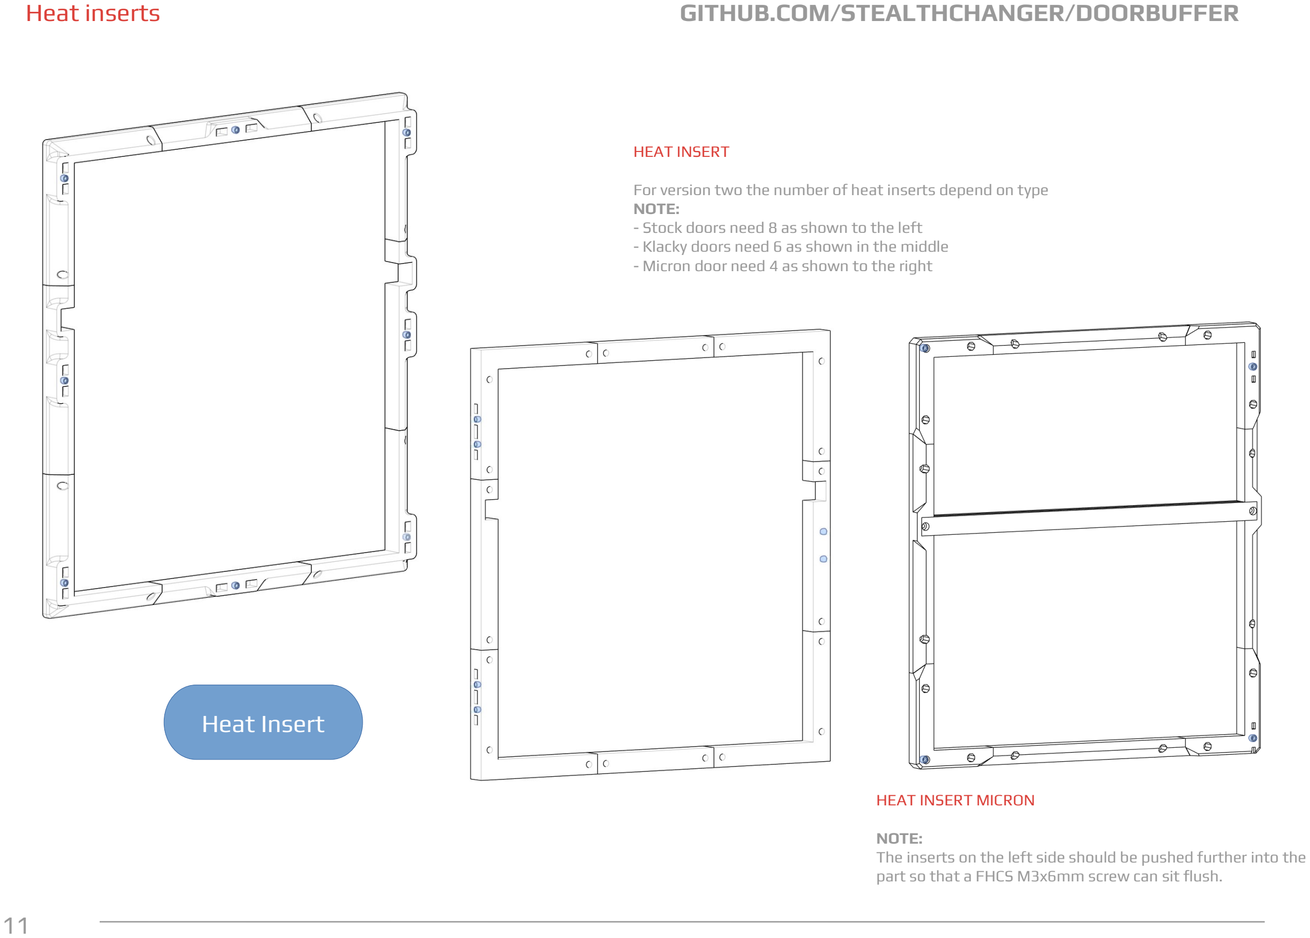
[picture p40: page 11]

HEAT INSERT

For version two the number of heat inserts depend on type NOTE:
- Stock doors need 8 as shown to the left
- Klacky doors need 6 as shown in the middle
- Micron door need 4 as shown to the right

11

## Heat Insert

HEAT INSERT MICRON

NOTE:
The inserts on the left side should be pushed further into the part so that a FHCS M3x6mm screw can sit flush.

## Attach to frame

## M3x8 SHCS

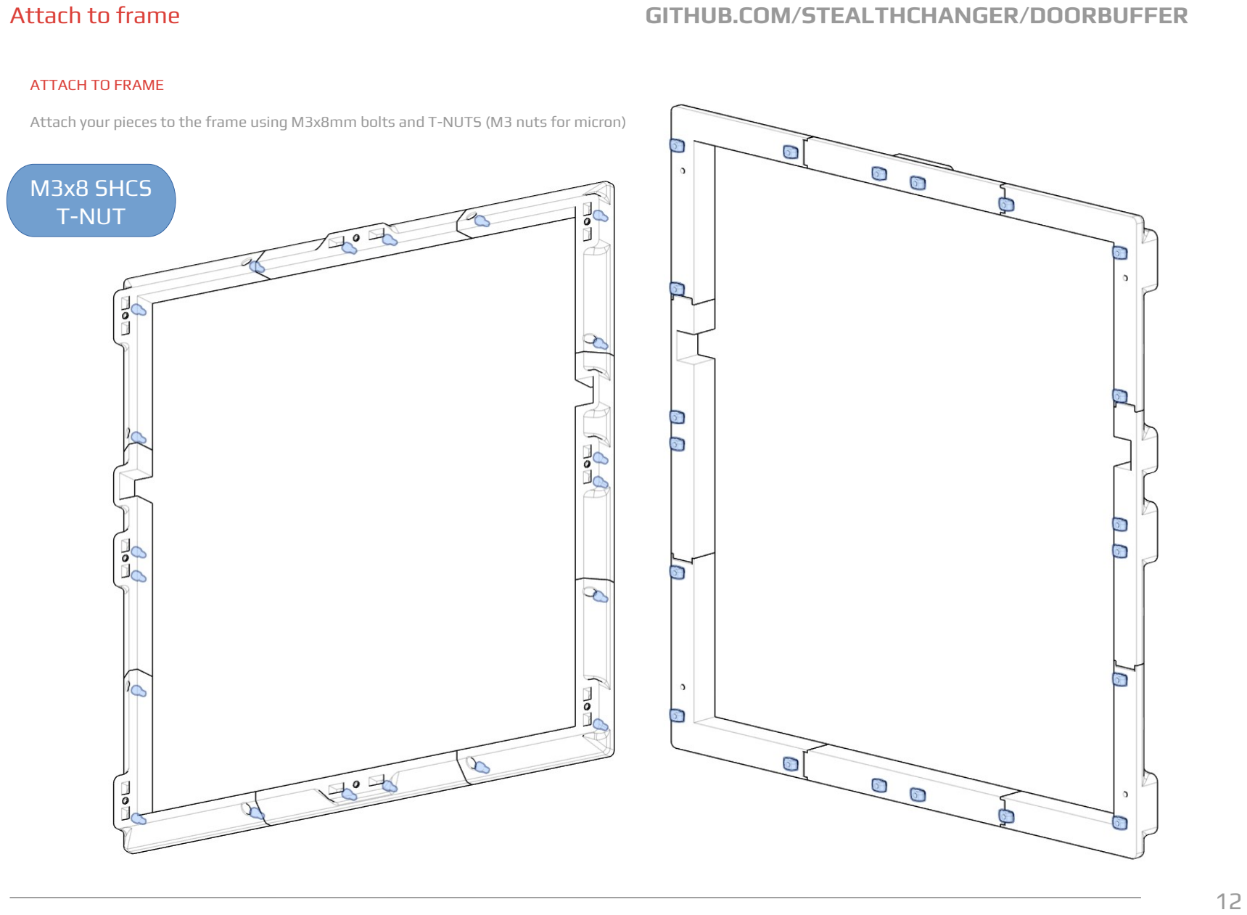
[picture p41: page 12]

ATTACH TO FRAME

Attach your pieces to the frame using M3x8mm bolts and T-NUTS (M3 nuts for micron)

12

## T-NUT

## MOUNT DOORS

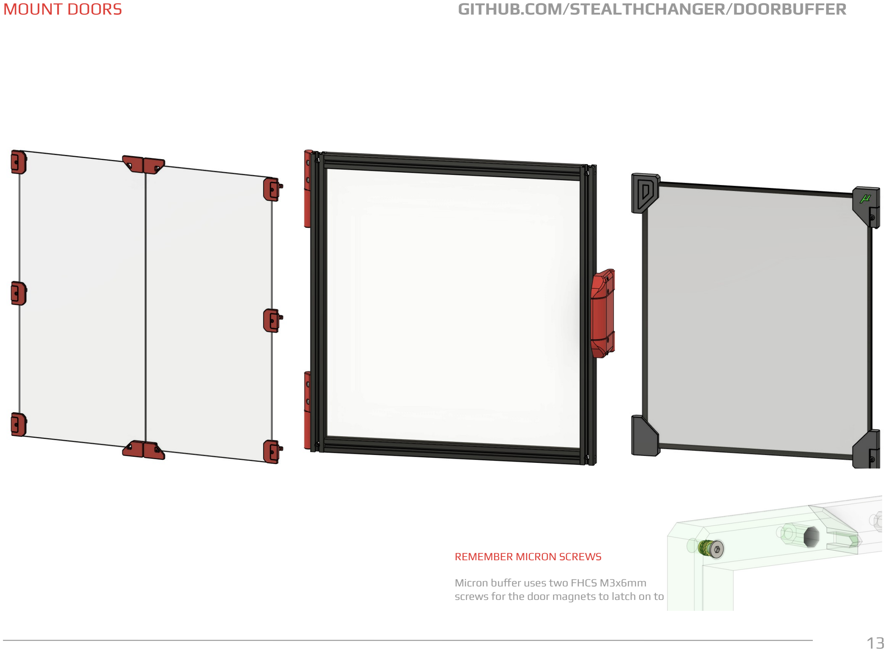
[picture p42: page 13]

13

REMEMBER MICRON SCREWS

Micron buffer uses two FHCS M3x6mm screws for the door magnets to latch on to

## SIDE PIECE

## IMPORTANT NOTE FOR STOCK DOORS

Some combinations of size and dockheight can result in the middle door hinge clipping into dock extrusion. To remedy this, snip off the highlighted area.

14

## Interference

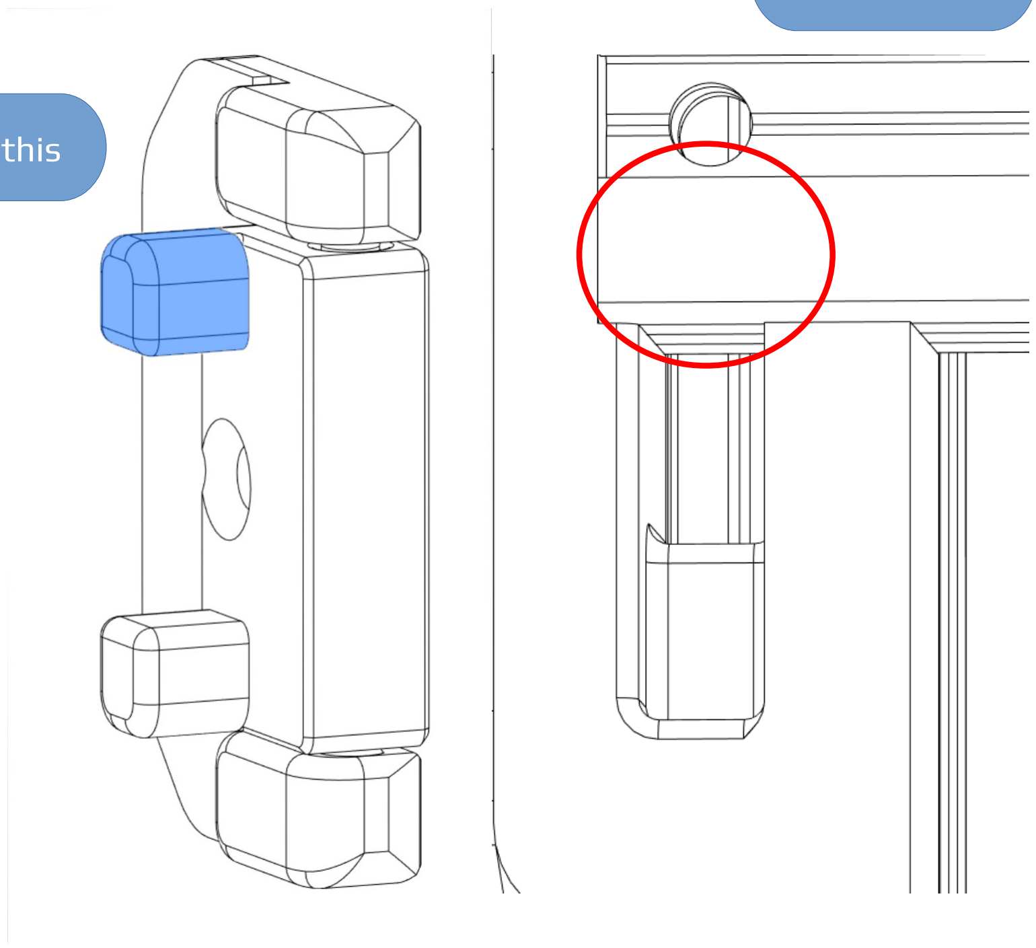
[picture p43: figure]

## Remove this

## PARAMETRIC EDITING

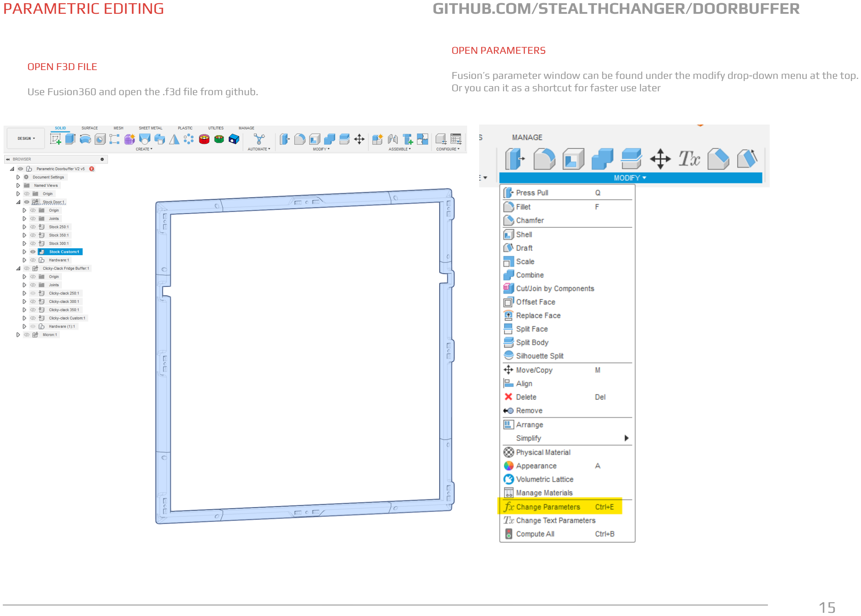
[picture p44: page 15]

15

OPEN F3D FILE

Use Fusion360 and open the .f3d file from github.

OPEN PARAMETERS

Fusion’s parameter window can be found under the modify drop-down menu at the top. Or you can it as a shortcut for faster use later

## EDITING PARAMETERS

PARAMETERS

Edit the numbers inside the red box (under the expression column)

NOTE: Numbers are capped to not go below a 250 size.

16

Default parameters | Frame_Z | Frame_X
250mm Bed | 430mm | 410mm
300mm Bed | 480mm | 460mm
350mm Bed | 530mm | 510mm

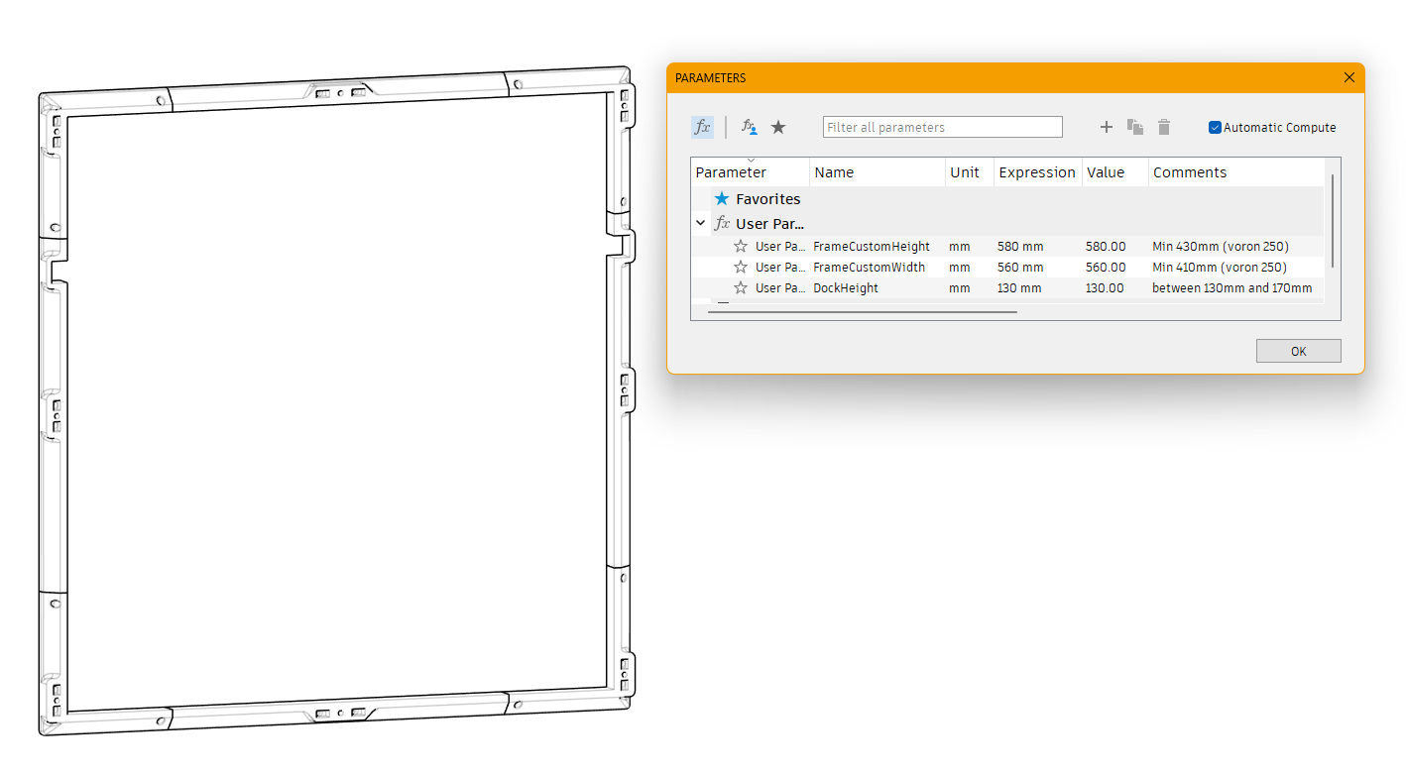
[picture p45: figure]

## SAVE STL’S

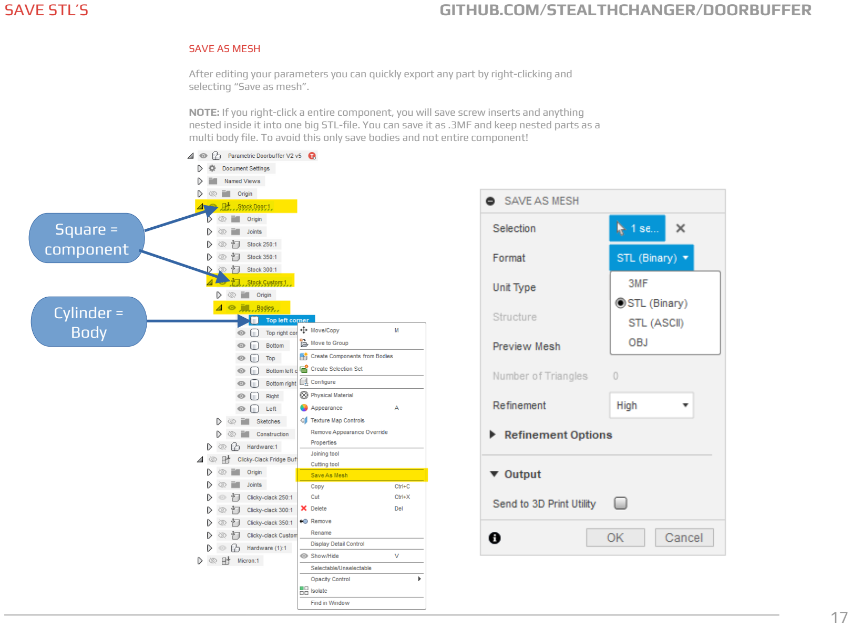
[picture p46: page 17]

SAVE AS MESH

After editing your parameters you can quickly export any part by right-clicking and selecting “Save as mesh”.

NOTE: If you right-click a entire component, you will save screw inserts and anything nested inside it into one big STL-file. You can save it as .3MF and keep nested parts as a multi body file. To avoid this only save bodies and not entire component!

17

## Square = component

## Cylinder = Body

## NEXT STEPS

ASSEMBLY COMPLETED!

NOTE: In case you forgot to install your modular docks, you can simply loosen the top middle piece and slide in the docks.

### https://github.com/Stealthchanger/DoorBuffer

18

Enjoy your new front door

19

# STEALTHCHANGER

GITHUB

github.com/StealthChanger

DISCORD

discord.gg/Mx9JKbt7

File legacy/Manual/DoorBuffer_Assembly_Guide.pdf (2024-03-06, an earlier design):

# Door Buffer

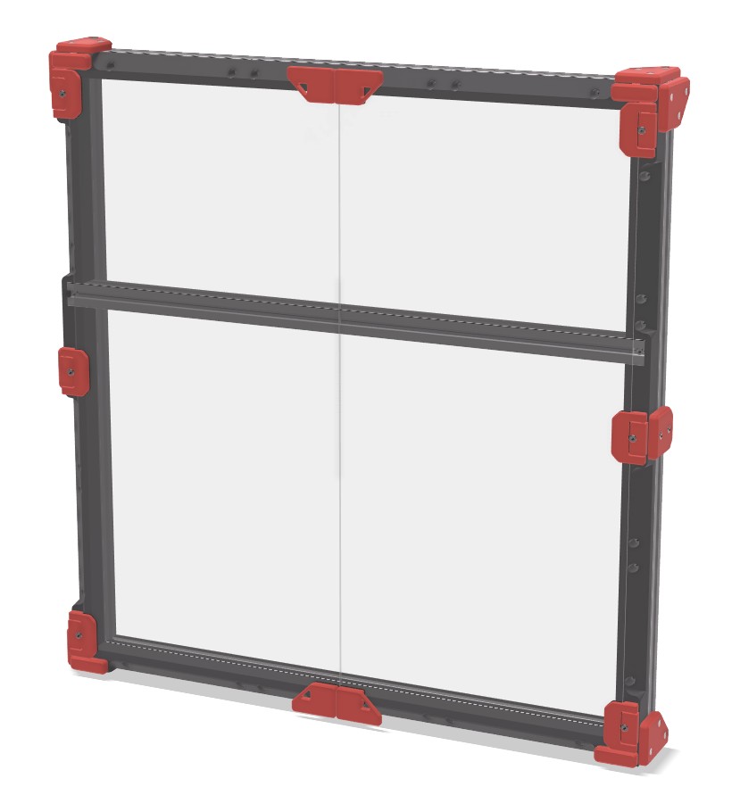
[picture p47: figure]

# Door Buffer BUILD GUIDE

# Giving you 20mm back, and a more rigid dock

# VERSION 2024-03-04

## PREFACE


Before you begin on your journey, a word of caution.

In the comfort of your own home you are about to assemble a robot. This machine can maim, burn, and electrocute you if you are not careful. Please do not become the first STEALTHCHANGER fatality. There is no special Reddit flair for that.

Please, read the entire manual before you start assembly. As you begin wrenching, please check our Discord channels for any tips and questions that may halt your progress.

Most of all, good luck!

THE STEALTHCHANGER TEAM

# GITHUB.COM/STEALTHCHANGER/DOORBUFFER

## TABLE OF CONTENTS

Introduction | 04
Hardware | 07
Shuttle | 08
Stealthburner | 11
Dragonburner | 14
Attaching to Carriage | 17
End Stop Options | 21
Next Steps | 22

## INTRODUCTION

PART PRINTING GUIDELINES

The Voron Team has provided the following print guidelines for you to follow in order to have the best chance at success with your parts. The StealthChanger Team recommends to follow the same standards. There are often questions about substituting materials or changing printing standards, but we recommend you follow these:

3D PRINTING PROCESS
Fused Deposition Modeling (FDM)

MATERIAL
ABS

LAYER HEIGHT
Recommended: 0.2mm

EXTRUSION WIDTH
Recommended: Forced 0.4mm

INFILL TYPE
Grid, Gyroid, Honeycomb, Triangle or Cubic

INFILL PERCENTAGE
Recommended: 15% or higher

NOTE: These parts do not experience any load an can be less dense compared to other Voron parts

WALL COUNT
Recommended: 4

SOLID TOP/BOTTOM LAYERS
Recommended: 5

## INTRODUCTION

FILE NAMING

By this time you should have already downloaded our STL files from the StealthChanger GitHub. You might have noticed that we have used the Voron naming convention for the files. This is how to use them.

PRIMARY COLOUR

Example part_x4.stl

These files will have nothing at the start of the filename.

ACCENT COLOUR

Example [a]_part.stl

We have added “[a]” to the front of any STL file that is intended to be printed with accent colour.

QUANTITY REQUIRED

Example [a]_part_x4.stl

If any file ends with “_x#”, that is telling you the quantity of that part required to build the machine.

HOW TO GET HELP

If you need assistance with your build, we are here to help. Head on over to our Discord group and post your questions. This is our primary medium to help STEALTHCHANGER Users and we have a great community that can help you out if you get stuck.

### https://discord.gg/Mx9JKbt7

## INTRODUCTION

REPORTING ISSUES

Should you find an issue in the documentation or have a suggestion for an improvement please consider opening an issue on GitHub (https://github.com/Stealthchanger/DoorBuffer/issues). When raising an issue please include the relevant page numbers and a short description; annotated screenshots are also very welcome. We periodically update the manual based on the feedback we get.

THIS IS JUST A REFERENCE

This manual is designed to be a simple reference manual and we always recommend downloading the cad-files to look around for yourself.

### https://github.com/Stealthchanger/DoorBuffer

## HARDWARE REFERENCE


MAGNET Metric round button neodymium magnet used on the Voron. N52 is highly recommended. | SOCKET HEAD CAP SCREW (SHCS) Metric fastener with a cylindrical head and hex drive. The most common fastener used on the Voron. ISO 4762


T-NUT Hammerhead A type of nut that slides into the extrusion rail as a method of affix other parts to it. | HEAT SET INSERT Heat inserts with a soldering tip so that they melt the plastic when installed. As the plastic cools, it solidifies around the knurls and ridges on the insert for excellent resistance to both torque and pull-out.

## FRAME


BASE FRAME

This build is meant to attach onto a normal 2020 V2.4 frame, though if you have a customized one there will be instructions on how to edit this entire design in Fusion360 at the end.

TOOLBAR HOLE PLACEMENT

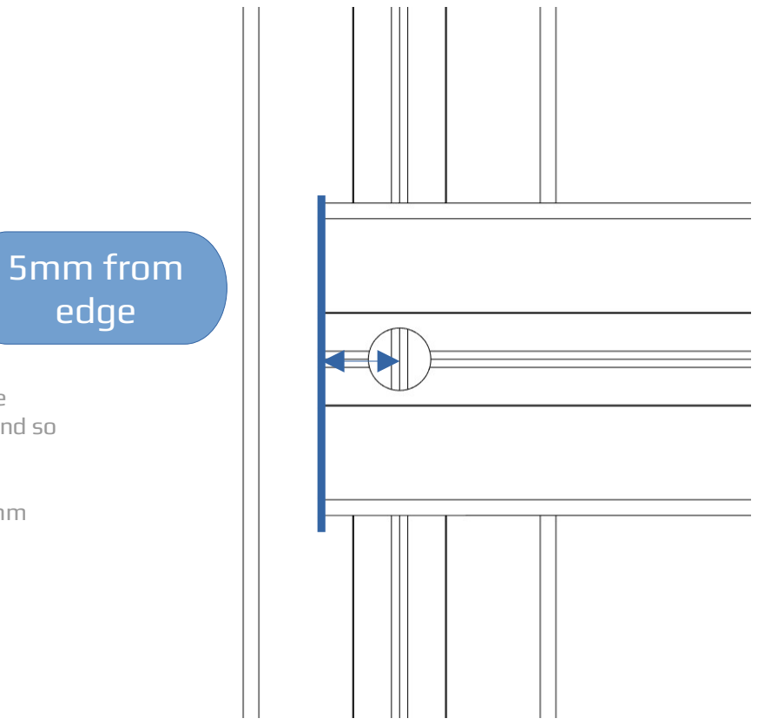
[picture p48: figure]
5mm from edge

The bottom bar that the modular docks mount to is 10mm shorter than your frame measured furthest left to right. A standard 350 frame is 510mm across the front and so the toolbar needs to be 500mm

NOTE: You will need to drill a hole big enough for a 3mm screw to pass through 4mm minimum is recommended for better adjustment.

## FRAME

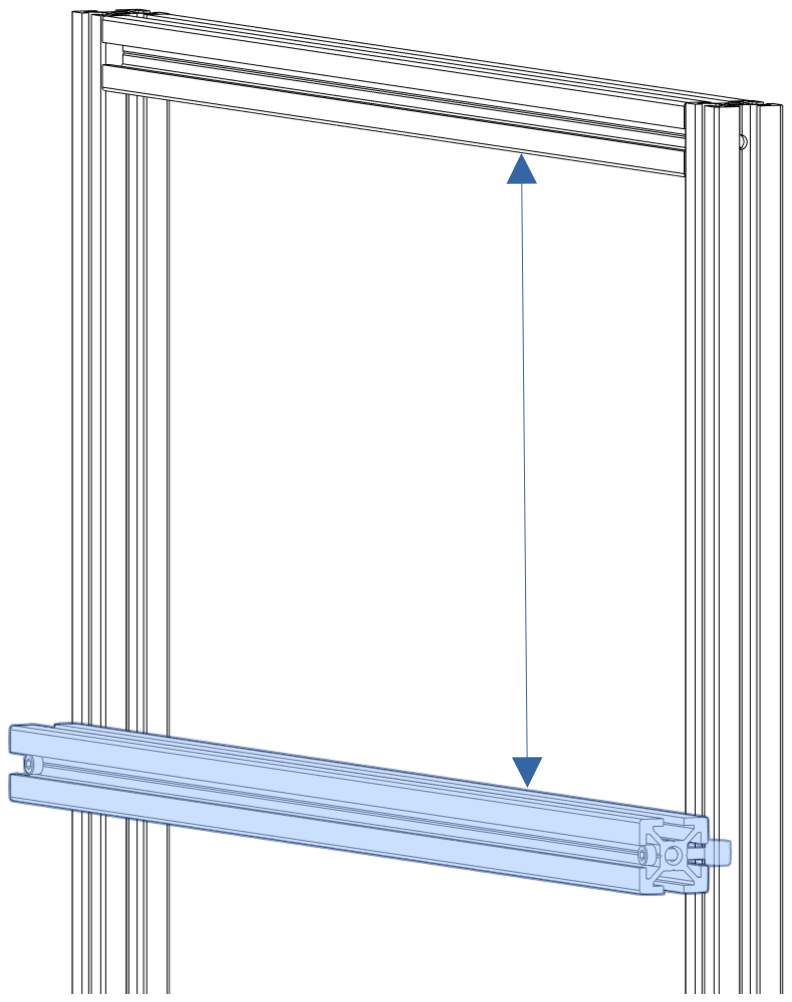
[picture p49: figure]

TOOLBAR TO FRAME

Bolt on the toolbar extrusion 170mm down so that there is a 170mm free clearing between them.

170mm

SCREWS

Take your M3x20mm through the holes you made and mount it using T-NUT’s

## M3x20mm SHCS T-NUT

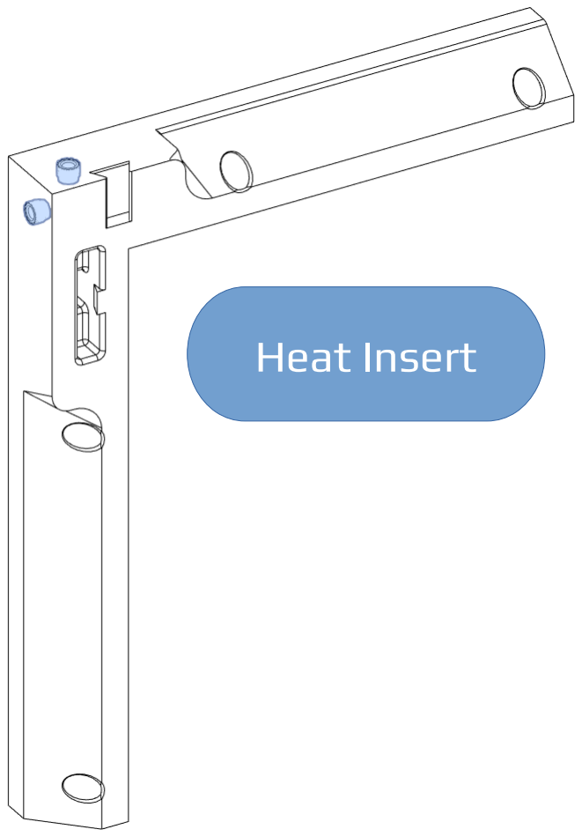
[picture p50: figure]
Heat Insert

HEAT INSERT (optional)

These corner inserts are meant for the larger panel clips provided. You do not need them in case you don't wish to reprint your excising panel clips.

## CORNER PIECE

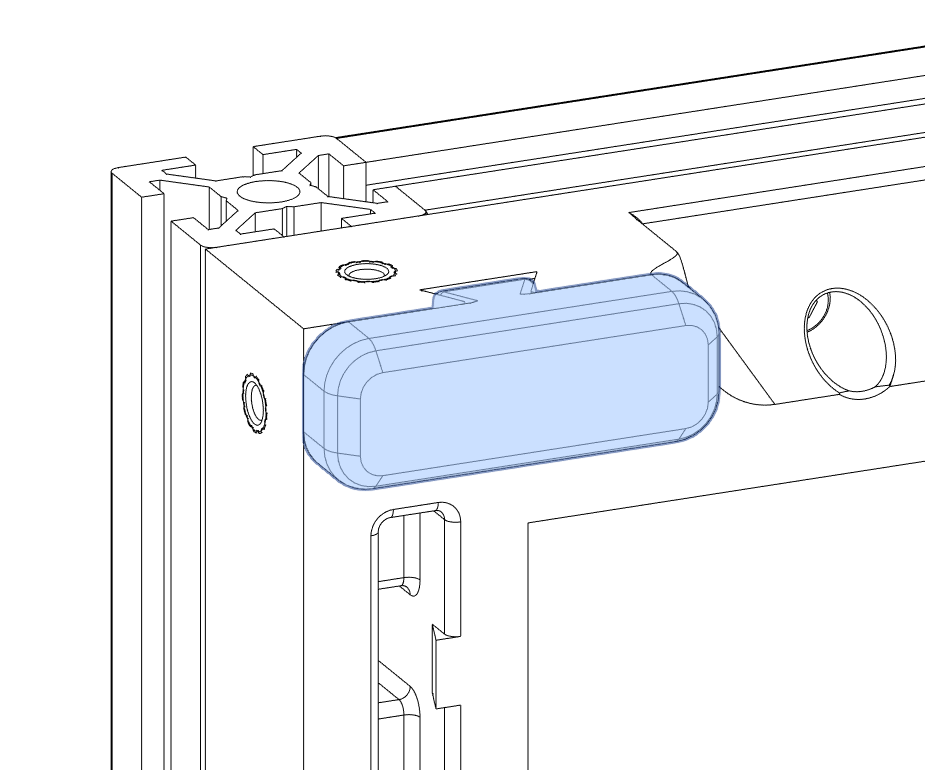
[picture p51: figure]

FAKE CLIP (optional)

The fake clip is purely cosmetic and not obligatory (it looks nice tho).

## CORNER PIECE

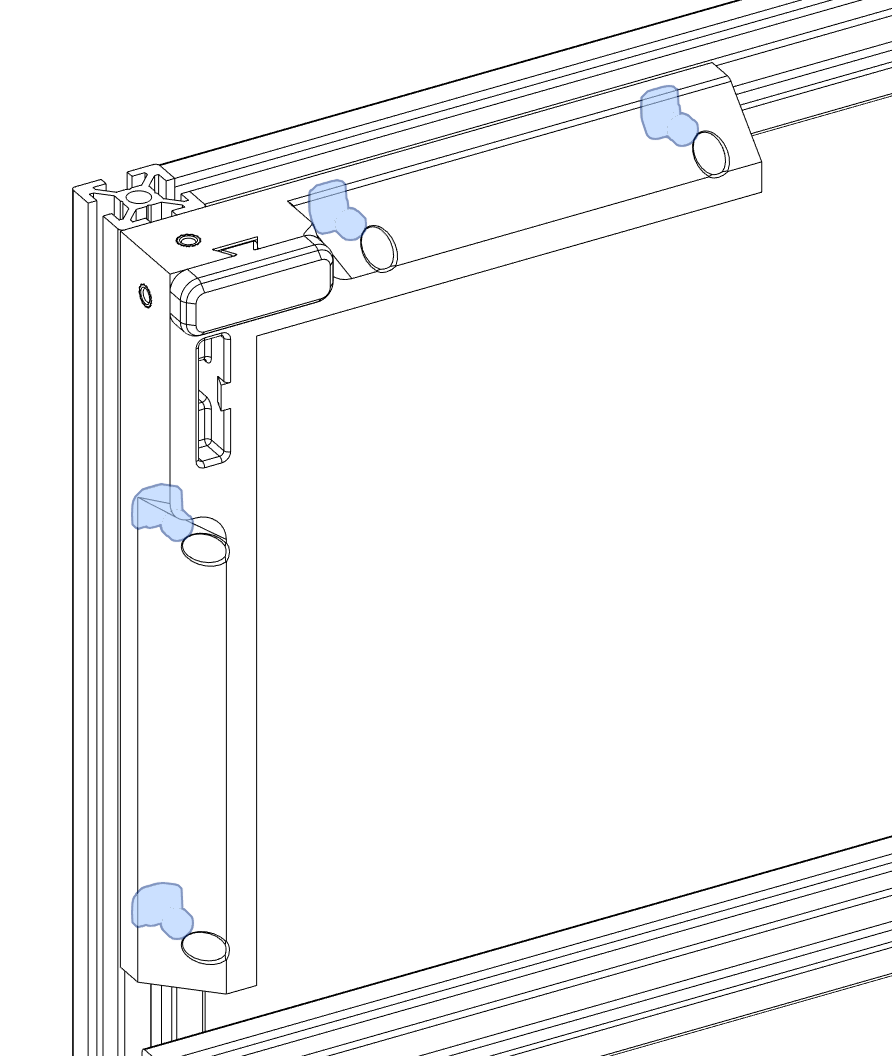
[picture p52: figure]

ATTACH TO FRAME

Attach your corner piece to the frame using 4 M3x8mm bolts and 4 T-NUTS

ATTACH PANEL CLIPS (optional)

The elongated panelclips are identical to stock Voron except you will need 1 aditional M3x8 SHCS bolt that attaches to the heat insert.

## M3x8 SHCS T-NUT

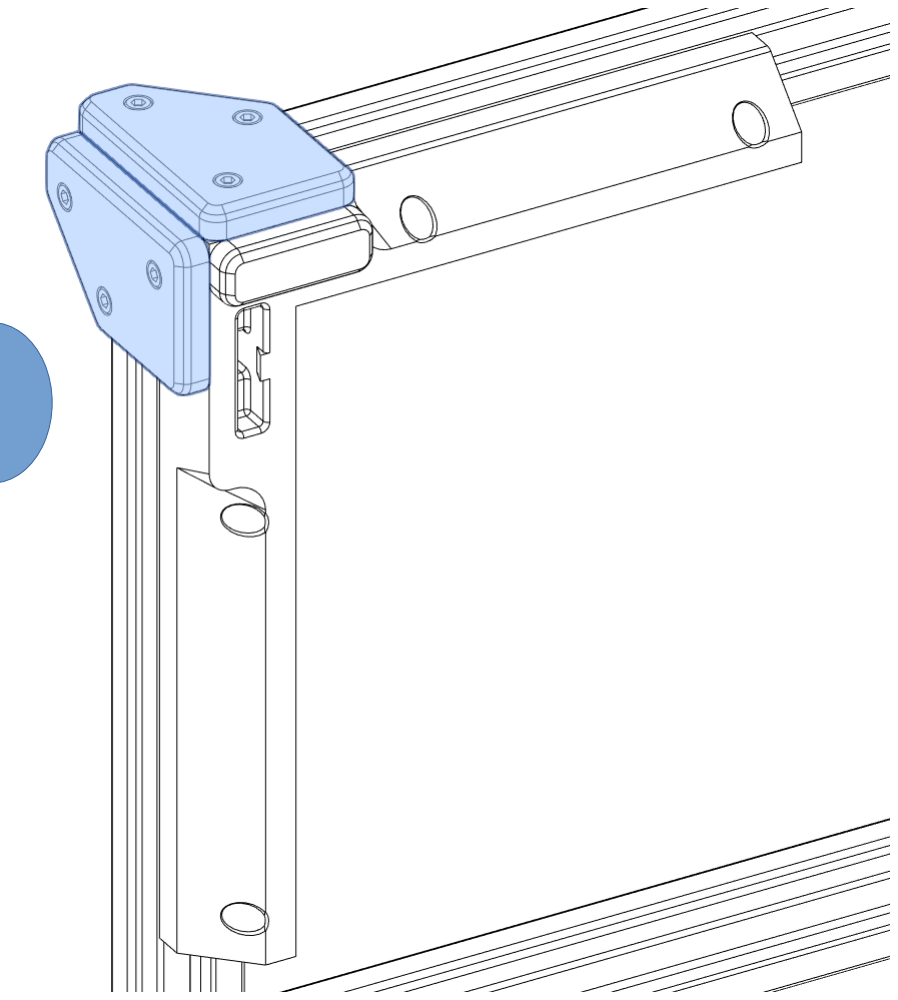
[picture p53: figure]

## M3x8 SHCS T-NUT

## SIDE PIECE

## IMPORTANT NOTE

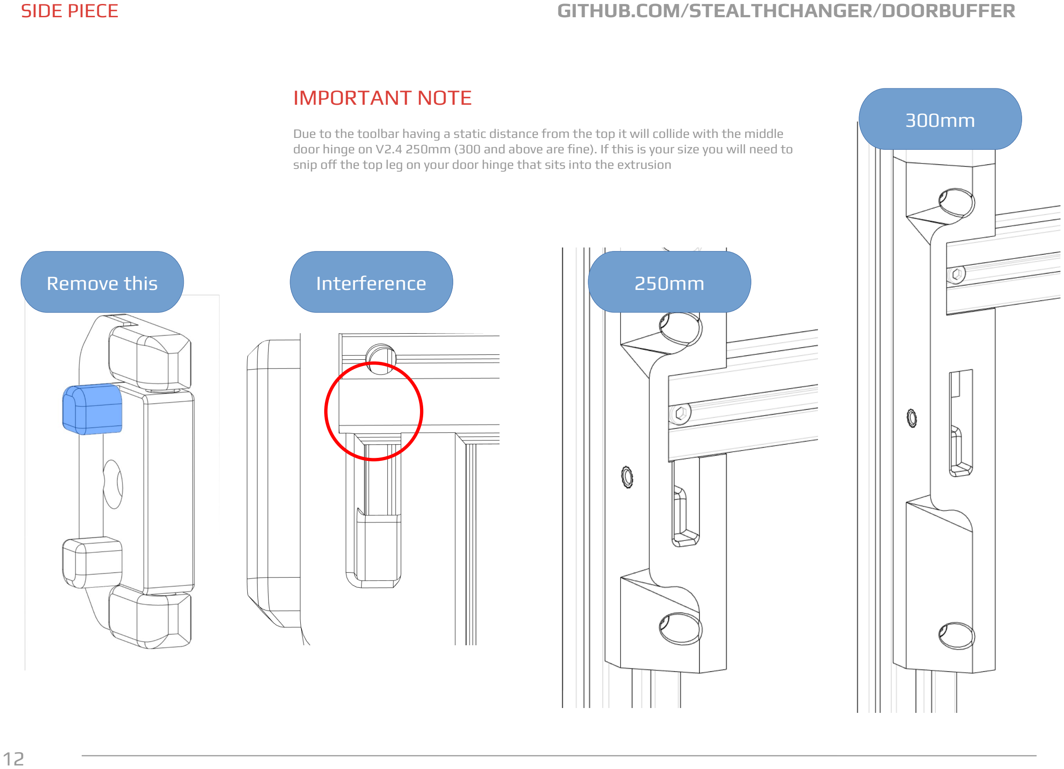
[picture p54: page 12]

Due to the toolbar having a static distance from the top it will collide with the middle door hinge on V2.4 250mm (300 and above are fine). If this is your size you will need to snip off the top leg on your door hinge that sits into the extrusion

250mm

300mm

Remove this | Interference

## SIDE PIECE

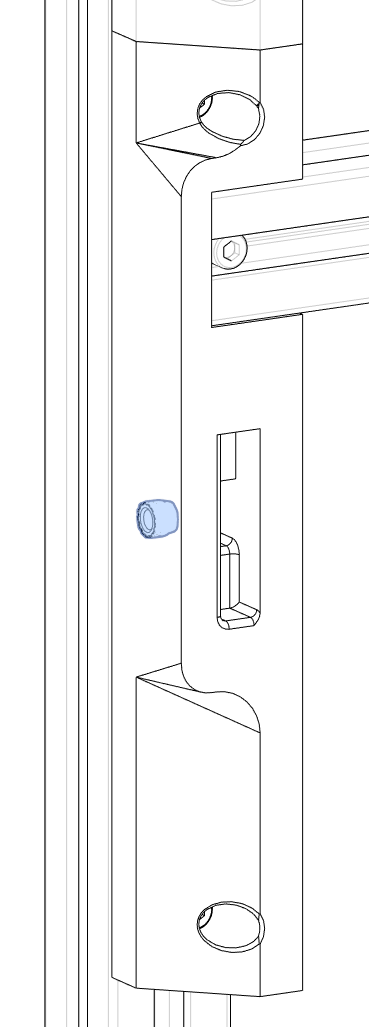
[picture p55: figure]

HEAT INSERT

Optional heat insert for elongated middle clip

ATTACH TO FRAME

Attach the side piece to your frame using 2 M3x8 SHCS and 2 T-NUT’s

## Heat Insert

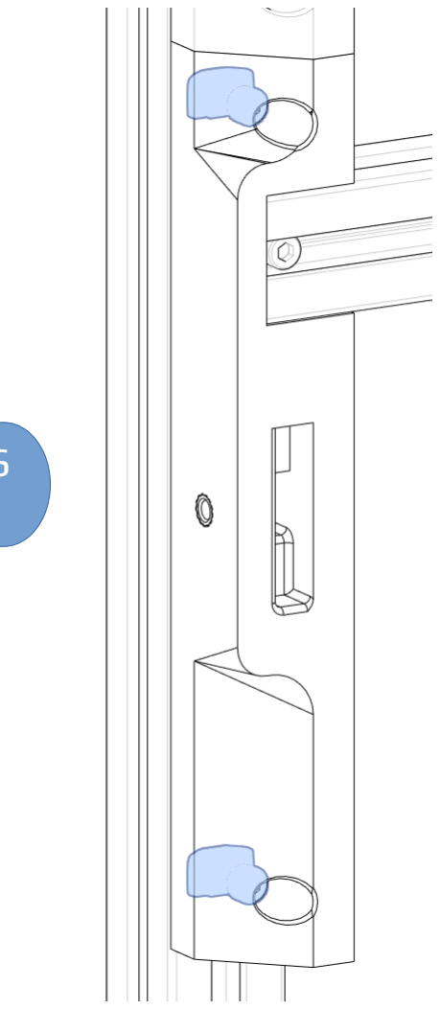
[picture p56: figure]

## M3x8 SHCS T-NUT

## TOP PIECE

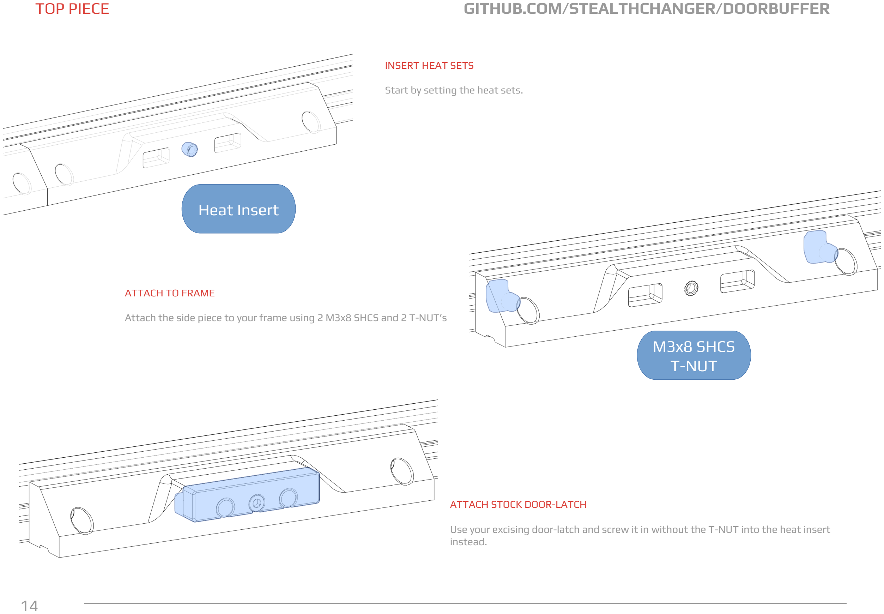
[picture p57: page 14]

INSERT HEAT SETS

Start by setting the heat sets.

ATTACH TO FRAME

Attach the side piece to your frame using 2 M3x8 SHCS and 2 T-NUT’s

## Heat Insert

## M3x8 SHCS T-NUT

ATTACH STOCK DOOR-LATCH

Use your excising door-latch and screw it in without the T-NUT into the heat insert instead.

## REST OF FRAME

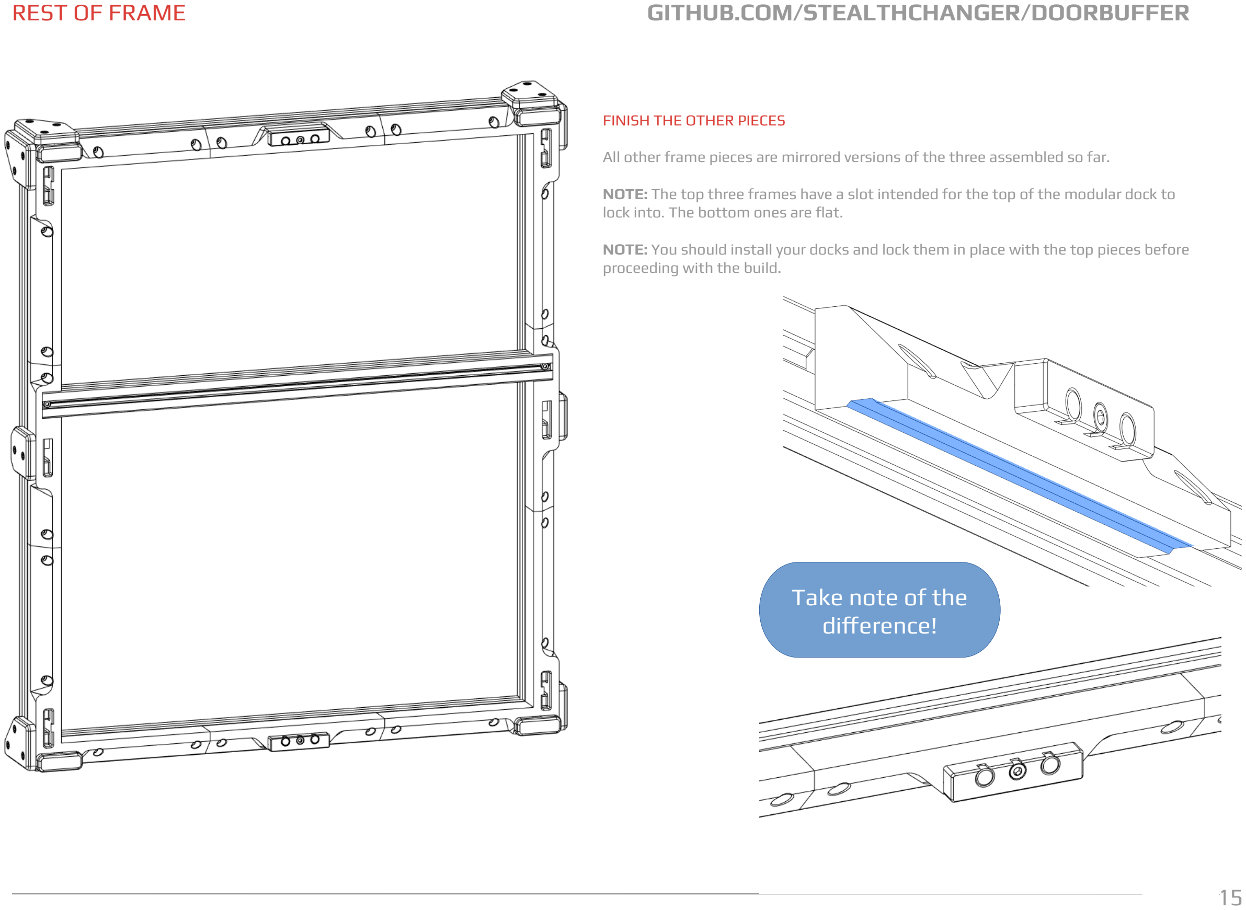
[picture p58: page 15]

FINISH THE OTHER PIECES

All other frame pieces are mirrored versions of the three assembled so far.

NOTE: The top three frames have a slot intended for the top of the modular dock to lock into. The bottom ones are flat.

NOTE: You should install your docks and lock them in place with the top pieces before proceeding with the build.

## Take note of the difference!

## DOORS

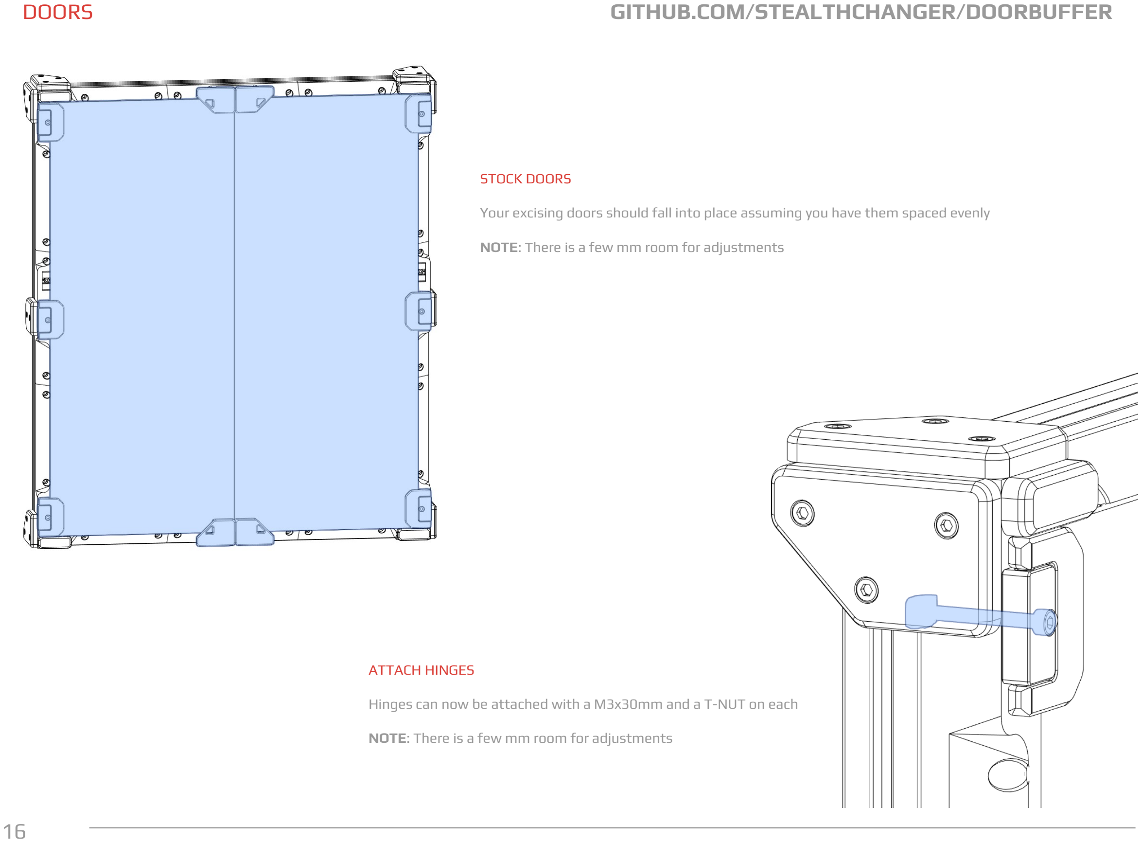
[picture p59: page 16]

STOCK DOORS

Your excising doors should fall into place assuming you have them spaced evenly

NOTE: There is a few mm room for adjustments

ATTACH HINGES

Hinges can now be attached with a M3x30mm and a T-NUT on each

NOTE: There is a few mm room for adjustments

## PARAMETRIC EDITING

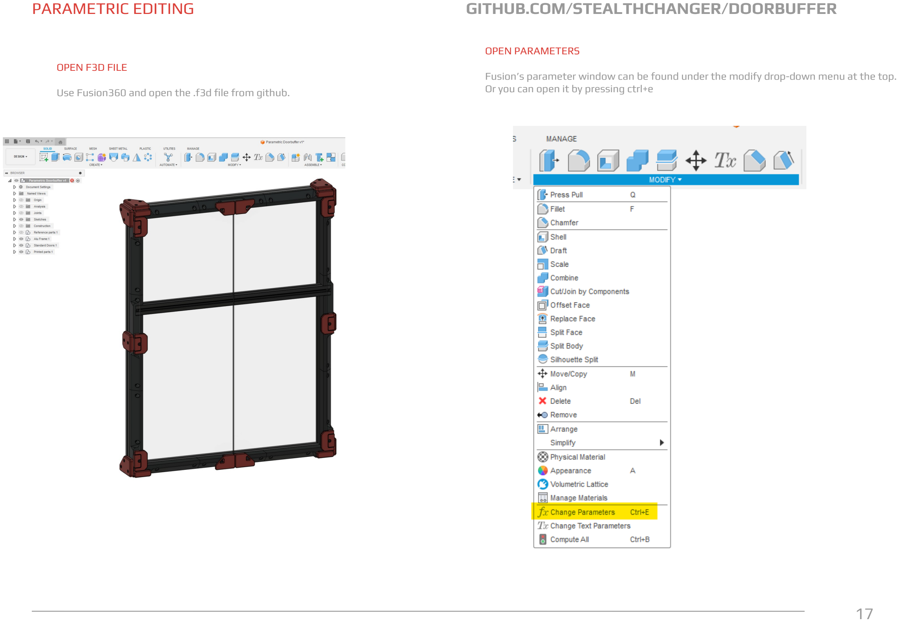
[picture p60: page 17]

OPEN F3D FILE

Use Fusion360 and open the .f3d file from github.

OPEN PARAMETERS

Fusion’s parameter window can be found under the modify drop-down menu at the top. Or you can open it by pressing ctrl+e

## EDITING PARAMETERS

PARAMETERS

Edit the numbers inside the red box (under the expression column)

WARNING! Do not input lower numbers than a 250mm bed it will break stuff!

Default parameters | Frame_Z | Frame_X
250mm Bed | 430mm | 410mm
300mm Bed | 480mm | 460mm
350mm Bed | 530mm | 510mm

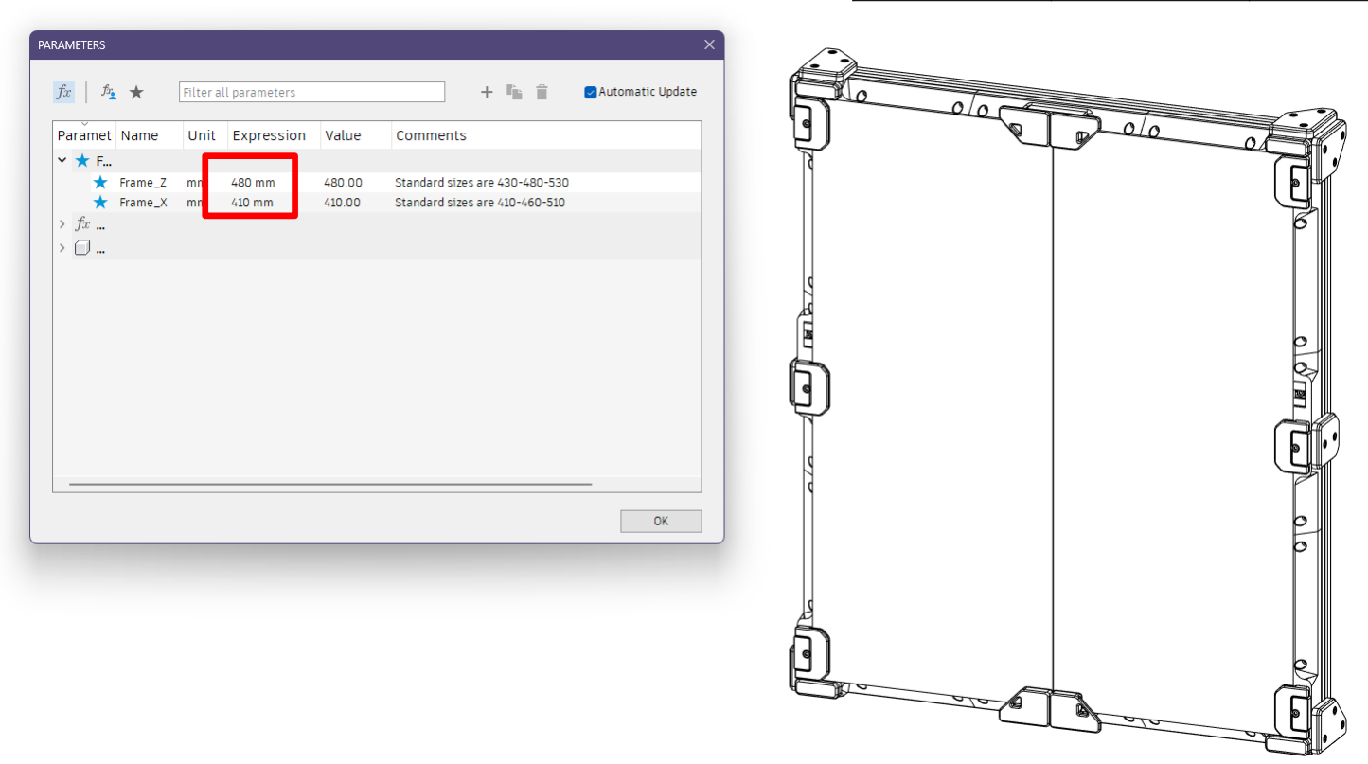
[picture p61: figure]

## SAVE STL’S

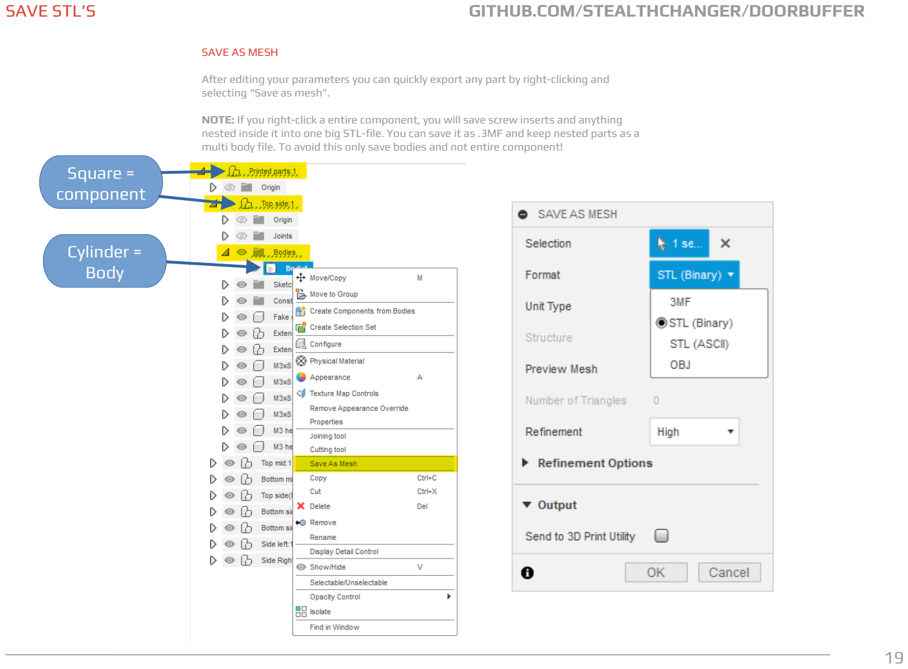
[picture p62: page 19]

SAVE AS MESH

After editing your parameters you can quickly export any part by right-clicking and selecting “Save as mesh”.

NOTE: If you right-click a entire component, you will save screw inserts and anything nested inside it into one big STL-file. You can save it as .3MF and keep nested parts as a multi body file. To avoid this only save bodies and not entire component!

## Square = component

## Cylinder = Body

## NEXT STEPS

ASSEMBLY COMPLETED!

NOTE: In case you forgot to install your modular docks, you can simply loosen the top middle piece and slide in the docks.

### https://github.com/Stealthchanger/DoorBuffer

Enjoy your new front door

# STEALTHCHANGER

GITHUB

github.com/StealthChanger

DISCORD

discord.gg/Mx9JKbt7

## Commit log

2024-03-07 Delete STL/[a]/.md
    Remove Extra file
2024-03-07 Delete STL/350/.md
    Remove Extra File
2024-03-07 Delete STL/300/.md
    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
2024-03-07 Delete STL/250/.md
    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
2024-03-07 These shouldn't be in a directory
    [[a]_Door_Hinge_x6.stl, [a]_Elongated_Corner_A_4mm_x3.stl, [a]_Elongated_Corner_B_4mm_x3.stl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]
2024-03-07 Delete CAD/.foo
    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
2024-03-09 Added BOM
2024-05-03 fixed top/bottom middle bar issue
    [Bottom_Middle.stl, Top_Middle.stl]
2024-05-14 Create 2020 3mm Hole Jig.stl
    Jig for drilling mounting hole in ends of 2020 crossbar
    [2020 3mm Hole Jig.stl]
2024-06-02 Add Short Frame Dock Mod
    [300_Left.f3d, 300_Left_vslot.f3d, 300_left.stl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]
2024-09-12 Add Doorbuffer Adapters
    [1515_doorbuffer_adapter.stl, 2020_doorbuffer_adapter.stl, Doorbuffer_Adapters.step]
2024-09-12 Rename files and redo the step file with proper names
    [1515_doorbuffer_adapter_x2.stl, 2020_doorbuffer_adapter_x2.stl, Doorbuffer_Adapters.step]
2024-09-12 Update to add a little more room for other types of extrusions
    [2020_doorbuffer_adapter_x2.stl, Doorbuffer_Adapters.step]
2024-09-29 added version 2 moved v1 to legacy
    [2020 3mm Hole Jig.stl, 300_Left.f3d, 300_Left_vslot.f3d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]
2024-09-29 added the printable dockbar
    [Micron dockbar.stl]
2024-09-30 2 hinge door buffer
    [Bottom Center.stl, Bottom Left.stl, Bottom Right.stl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]
2024-10-01 updated read me with an image too!
    [Bottom Center.stl, Bottom Left.stl, Bottom Right.stl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]
2024-10-15 fixed bottom left corner on stock 300, both version. Updated Cad files
    [Bottom left corner.stl]
2024-12-29 add monolith doorbuffer adapter
    add monolith doorbuffer adapter
    [2020_doorbuffer_adapter_monolith.step, 2020_doorbuffer_adapter_monolith.stl]
2025-02-09 Fixed folder names
    [BTT HDMI5 Mount forClicky-Clack Fridge Doorwith Door Buffer v2.3mf, ORIG - BTT HDMI5 Cable protector-Straight Through.stl, ORIG - BTT HDMI5 mount bracket.stl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]
2025-02-09 Reorganised files
    [BTT HDMI5 Mount forClicky-Clack Fridge Doorwith Door Buffer v2.3mf, ORIG - BTT HDMI5 Cable protector-Straight Through.stl, ORIG - BTT HDMI5 mount bracket.stl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]
2025-02-09 Added cover and cover inlay stl's.
    [DET-Man BTT HDMI5 Display Cover Logo Inlay.stl, DET-Man BTT HDMI5 Display Cover.stl]
2025-04-06 add usermod doorbuffer side door
    add usermod doorbuffer side door
    [2020_doorbuffer_adapter_blank_for_M5x16_BHCS_x2.step, 2020_doorbuffer_adapter_blank_for_M5x16_BHCS_x2.stl, NewLatchWithHandle_m2x10mmSHCS_screw_5.5mm_longboi v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]
2025-07-01 add usermod: Doorbuffer_Clicky-Clack_Side_Door (#11)
    * add usermod: Doorbuffer_Clicky-Clack_Side_Door
    add usermod: Doorbuffer_Clicky-Clack_Side_Door
    * Update README.md
    [doorbuffer-300-clickyclacky-sidedoor_A_v2.step, doorbuffer-300-clickyclacky-sidedoor_A_v2.stl, doorbuffer-300-clickyclacky-sidedoor_B_v2.step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]
2025-07-27 Move adaptor to main repo
    [1515_doorbuffer_adapter_x2.stl, 2020_doorbuffer_adapter_x2.stl, Doorbuffer_Adapters.step]
2026-02-18 stealthchanger website fix (#12)
    [Bottom Center.stl, Bottom Left.stl, Bottom Right.stl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]
